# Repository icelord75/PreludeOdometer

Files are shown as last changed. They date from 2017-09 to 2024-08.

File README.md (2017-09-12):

# PreludeOdometer

Dot matrix LED display replacement for mechanical odometer in Honda Prelude IV

## Supported modes:
 - Arduino Nano328 controller
 - Precise configure wheel/VSS ratio
 - Total mileage
 - A/B trip (up to 9999.9km)
 - Motor hours counter
 - Configurable LED needle illumination with dimming feature
 - Configurable Electroluminescence instrumental cluster illumination controller
 - Outside Temperature (DS1820 sensor)

## License

**PreludeOdometer** is available under GPL License.

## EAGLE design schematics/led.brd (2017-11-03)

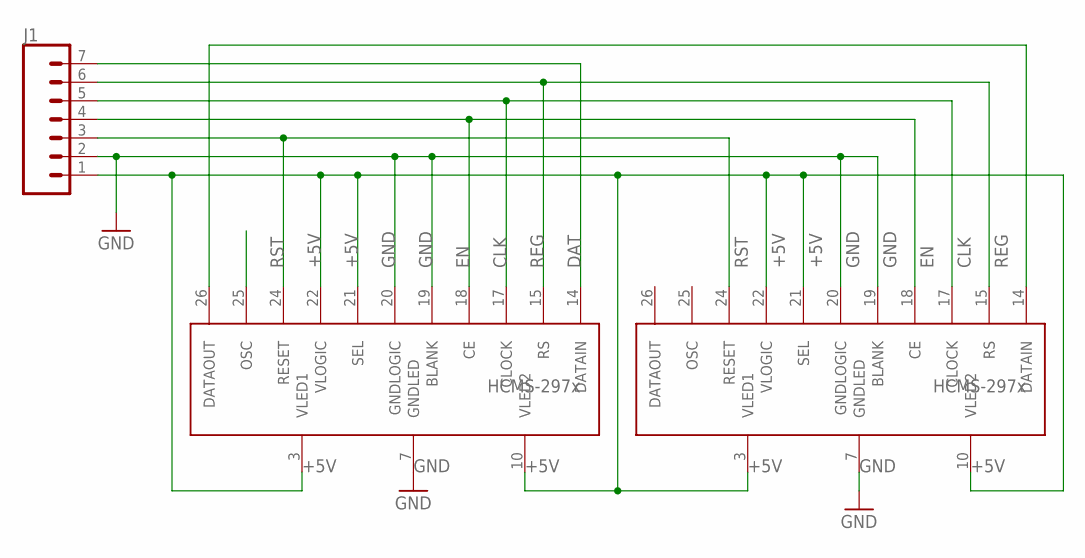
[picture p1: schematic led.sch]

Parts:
J1: CONN_07LONGPADS; 1X07_LONGPADS
U$1, U$2: HCMS-297X

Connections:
+5V: J1.1, U$1.3 (VLED1), U$1.10 (VLED2), U$1.21 (SEL), U$1.22 (VLOGIC), U$2.3 (VLED1), U$2.10 (VLED2), U$2.21 (SEL), U$2.22 (VLOGIC)
CLK: J1.5, U$1.17 (CLOCK), U$2.17 (CLOCK)
DAT: J1.7, U$1.14 (DATAIN)
EN: J1.4, U$1.18 (CE), U$2.18 (CE)
GND: J1.2, U$1.7 (GNDLED), U$1.19 (BLANK), U$1.20 (GNDLOGIC), U$2.7 (GNDLED), U$2.19 (BLANK), U$2.20 (GNDLOGIC)
unnamed: U$1.26 (DATAOUT), U$2.14 (DATAIN)
REG: J1.6, U$1.15 (RS), U$2.15 (RS)
RST: J1.3, U$1.24 (RESET), U$2.24 (RESET)

Board: 2 copper layers, 3 parts (0 on the bottom side), 8 nets, no tracks yet.

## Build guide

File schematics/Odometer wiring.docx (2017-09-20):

# MAIN BOARD

# 2 Pin SETUP BUTTON

1. Setup button
2. Setup button

# 3 Pin 1WIRE SENSOR

1. +5V
2. GND
3. 1WIRE

# 6 Pin CONNECTION BOARD

1. Button
2. LED DAT
3. LED REG
4. LED CLK
5. LED EN
6. LED RST

# 7 Pin CONNECTION BOARD

1. +12 IN
2. +5 OUT
3. DIM IN
4. VSS IN
5. NEEDLE CTL OUT
6. INDIGLO CTL OUT
7. GND

# CONNECTION BOARD

# 4 Pin GAUGES

1. +12 IN
2. DIM IN
3. VSS IN
4. GND IN

# 2 Pin NEEDLE

1. GND OUT
2. +5 OUT

# 3 Pin INDIGLO

1. N/C
2. GND OUT
3. +12 OUT

# 2 Pin #2 GAUGE BUTTON (next to 7PIN)

1. Button
2. Button

# 7 Pin LED MATRIX Display

1. +5V OUT
2. GND
3. LED RES
4. LED EN
5. LED CLK
6. LED REG
7. LED DAT

# 8 Pin MAIN BOARD

1. +12 OUT
2. +5 IN
3. VSS OUT
4. DIM OUT
5. NEEDLE CTL OUT
6. INDIGLO CTL OUT
7. –
8. GND

# 6 Pin MAIN BOARD

1. Button
2. LED DAT
3. LED REG
4. LED CLK
5. LED EN
6. LED RES

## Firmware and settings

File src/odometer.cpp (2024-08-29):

/*
   //      _______ __  _________ _________
   //      \_     |  |/  .  \   |   \ ___/
   //        / :  |   \  /   \  |   / _>_
   //       /      \ | \ |   /  |  /     \
   //      /   |___/___/____/ \___/_     /
   //      \___/--------TECH--------\___/
   //        ==== ABOVE SINCE 1994 ====
   //
   //   Ab0VE TECH - HONDA Prelude Odometer
 */

/* Controller connections
   //            +-----------+
   //            • TX    Vin •
   //            • RX  A Gnd •  <- GND
   //            • RST R RST •
   //     GND -> • GND D  +5 •  <- +5V Reg. LM2596HV
   //     VSS -> • 2   U  A7 •
   //     RPM -> • 3   I  A6 •
   // LED DAT <- • 4   N  A5 • -> FRAM SCL
   // LED Reg <- • 5   O  A4 • -> FRAM SDA
   // LED Clk <- • 6      A3 •
   //  LED En <- • 7   N  A2 •
   // LED RST -> • 8   A  A1 •
   //  Needle <- • 9   N  A0 • <- DIMMING
   // Indiglo <- • 10  O Arf •
   //   Setup -> • 11    3V3 •
   //  Button -> • 12 ||| 13 • <- OneWire DS1820
   //            +-----------+
 */

// TODO
//   racelogic bum edition )))
//   longterm l/100km
//   instant l/100km

//#define DEBUG

#include <avr/pgmspace.h>
#include <Arduino.h>
#include <LedDisplay.h>
#include <FM24.h>
#include <OneWire.h> // platformio lib install "OneWire"

#define disk1 0x50 // page of FM24C

OneWire ds(13); // DS1820 Temperature sensor

#define PPR 4 // VSS pulses per axle revolution

#define TRIP_A 0
#define TRIP_B 1
#define MOTOR_HOUR 2
#define OUTSIDE_TEMP 3

#define MAX_SHOW 3

// default tire size 205/55R15
#define TIRE_WIDTH_DEFAULT 4
#define TIRE_SIDE_DEFAULT 6
#define TIRE_RIM_DEFAULT 2

uint16_t TIRE_WIDTH_ARRAY[] = {165, 175, 185, 195, 205, 215, 225, 235, 245, 255, 265, 275, 285, 295, 305};
uint8_t TIRE_SIDE_ARRAY[] = {25, 30, 35, 40, 45, 50, 55, 60, 65, 70, 75, 80, 85};
uint8_t TIRE_RIM_ARRAY[] = {13, 14, 15, 16, 17, 18, 19, 20, 21, 22};

#define CONFIG_POS_MAX 11

// CONFIG
uint8_t TIRE_RIM;
uint8_t TIRE_WIDTH;
uint8_t TIRE_SIDE;
#define NEEDLE_STEP 16
#define NEEDLE_DIMMED_DEFAULT 127
#define NEEDLE_UNDIMMED_DEFAULT 255
uint8_t NEEDLE_DIMMED;
uint8_t NEEDLE_UNDIMMED;

#define MIN_DISPLAY 1 // Minimal visiable display
#define MAX_DISPLAY 15
#define DISPLAY_DIMMED_DEFAULT 10
#define DISPLAY_UNDIMMED_DEFAULT 15
uint8_t DISPLAY_DIMMED;
uint8_t DISPLAY_UNDIMMED;

#define INDIGLO_STEP 16
#define INDIGLO_DIMMED_DEFAULT 127
#define INDIGLO_UNDIMMED_DEFAULT 255
uint8_t INDIGLO_DIMMED;
uint8_t INDIGLO_UNDIMMED;

double TOTAL_TRIP;
double DAILY_TRIP_A;
double DAILY_TRIP_B;
int CURRENT_SHOW = TRIP_A;
boolean LEADING_ZERO;

// VSS input pin
#define VSS_PIN 2
unsigned int PULSES = 0;
float LENPERPULSE = 0;

// RPM input pin
#define RPM_PIN 3
volatile unsigned int RPM_COUNT = 0;
unsigned long timeold = 0;
unsigned int RPMs = 0;
float MOTOR_TIME;
unsigned int NOMINAL_RPM; // RPM with 1 hour == 1 motor hour
#define MAX_NOMINAL 6000
#define NOMINAL_STEP 200
float MOTOR_HOURS;
uint16_t MOTOR_HOURS_LIMIT;
#define DEFAULT_MOTOR_HOURS_LIMIT 200
#define MOTOR_HOURS_STEP 10
#define MAX_MOTOR_HOURS 1000
boolean LIMIT_BLINK = true;
uint8_t DIMMING;

// PINS CONFIG
#define BUTTON 12
#define NEEDLE 9
#define DIMPIN 14 // A0 as DIGITAL_PIN
#define SETUP_PIN 11
#define INDIGLO 10

#define LED_dataPin 4
#define LED_registerSelect 5
#define LED_clockPin 6
#define LED_enable 7
#define LED_reset 8
#define LED_displayLength 16 // Two HCMS-297x led matrix displays
LedDisplay myDisplay = LedDisplay(LED_dataPin, LED_registerSelect, LED_clockPin, LED_enable,
                                  LED_reset, LED_displayLength);

#define LOGO_DELAY 500 // first logo output delay
#define LONGPRESS_TIME 1000

float LEN = 0;
float TIRE_CIRCUMFERENCE;
float TEMPERATURE = 0;
unsigned long TIME, TIMES;
char buffer[20];
bool PRESSED = false;
bool LONGPRESS = false;
bool DIM = false;
bool DIMMED = true;
bool SETUP_PRESSED = false;
bool SETUP_DO = false;
uint8_t val;
uint8_t SETUP_POS = 0;
uint8_t data[12];
uint8_t addr[8];
uint8_t type_s;

#define DISPLAY_TRIP 0
#define DISPLAY_SETUP 1
uint8_t DISPLAY_MODE = DISPLAY_TRIP;
uint8_t DEFAULT_BRIGHTNESS;
uint8_t DEFAULT_NEEDLE;
uint8_t DEFAULT_INDIGLO;

bool result = false;

void CalcTire()
{
        TIRE_CIRCUMFERENCE = (TIRE_WIDTH_ARRAY[TIRE_WIDTH] * TIRE_SIDE_ARRAY[TIRE_SIDE] / 100 + TIRE_RIM_ARRAY[TIRE_RIM] * 25.4) * 3.1416 / 1000;
        LENPERPULSE = TIRE_CIRCUMFERENCE / PPR; // in Meters
#ifdef DEBUG
        Serial.print("TIRE CIRCUMFERENCE: ");
        Serial.print(TIRE_CIRCUMFERENCE);
        Serial.println("m");
        Serial.print("LEN PER PULSE: ");
        Serial.print(LENPERPULSE);
        Serial.println("m");
#endif
}

void VSS() // VSS signal interrupt
{
        PULSES++;
}

void RPM() // VSS signal interrupt
{
        RPM_COUNT++;
}

void setBrightness(uint8_t bright)
{
        // set the brightness: for each 4 chars
        for (int a = 1; a < LED_displayLength / 4; a++)
                myDisplay.loadControlRegister(B01110000 + (bright & B00001111));
}

void setup()
{
        Serial.begin(115200);
        Serial.print("\n\nAb0VE-TECH\nHonda Prelude Oddometer\n\n");
#ifdef DEBUG
        Serial.print("Connecting EEPROM...");
#endif
        twi_start();
#ifdef DEBUG
        Serial.print("OK\n");
#endif
        myDisplay.begin();
        setBrightness(0);
        pinMode(DIMPIN, INPUT);
        pinMode(NEEDLE, OUTPUT);
        pinMode(INDIGLO, OUTPUT);
        pinMode(BUTTON, INPUT_PULLUP);
        pinMode(SETUP_PIN, INPUT_PULLUP);
        pinMode(VSS_PIN, INPUT_PULLUP);
        pinMode(RPM_PIN, INPUT_PULLUP);

        attachInterrupt(digitalPinToInterrupt(VSS_PIN), VSS, RISING);  // positive tiggering
        attachInterrupt(digitalPinToInterrupt(RPM_PIN), RPM, FALLING); // negative tiggering

        // Start DS
        if (!ds.search(addr))
                ds.reset_search();
        if (addr[0] == 0x10)
                type_s = 1;
        else
                type_s = 0;
        ds.reset();
        ds.select(addr);
        ds.write(0x44, 1);

#ifdef DEBUG
        Serial.print("Reading config...");
#endif
        // read config from EEPROM
        result = FM24C_read(disk1, 0, (uint8_t *)&TOTAL_TRIP, 4);
        result = FM24C_read(disk1, 4, (uint8_t *)&DAILY_TRIP_A, 4);
        result = FM24C_read(disk1, 9, (uint8_t *)&DAILY_TRIP_B, 4);
        result = FM24C_read(disk1, 200, (uint8_t *)&CURRENT_SHOW, 1);
        result = FM24C_read(disk1, 37, (uint8_t *)&TIRE_WIDTH, 1);
        result = FM24C_read(disk1, 18, (uint8_t *)&TIRE_SIDE, 1);
        result = FM24C_read(disk1, 19, (uint8_t *)&TIRE_RIM, 1);
        result = FM24C_read(disk1, 20, (uint8_t *)&NEEDLE_DIMMED, 1);
        result = FM24C_read(disk1, 21, (uint8_t *)&NEEDLE_UNDIMMED, 1);
        result = FM24C_read(disk1, 22, (uint8_t *)&DISPLAY_DIMMED, 1);
        result = FM24C_read(disk1, 23, (uint8_t *)&DISPLAY_UNDIMMED, 1);
        result = FM24C_read(disk1, 24, (uint8_t *)&MOTOR_HOURS, 4);
        result = FM24C_read(disk1, 28, (uint8_t *)&NOMINAL_RPM, 4);
        result = FM24C_read(disk1, 32, (uint8_t *)&MOTOR_HOURS_LIMIT, 2);
        result = FM24C_read(disk1, 34, (uint8_t *)&LEADING_ZERO, 1);
        result = FM24C_read(disk1, 35, (uint8_t *)&INDIGLO_DIMMED, 1);
        result = FM24C_read(disk1, 36, (uint8_t *)&INDIGLO_UNDIMMED, 1);

#ifdef DEBUG
        Serial.print("EEPROM TOTAL: ");
        Serial.print(TOTAL_TRIP);
        Serial.print(", A: ");
        Serial.print(DAILY_TRIP_A);
        Serial.print(", B: ");
        Serial.print(DAILY_TRIP_B);
        Serial.print('\n');
        Serial.print("EEPROM TIRES: ");
        Serial.print(TIRE_WIDTH);
        Serial.print("/");
        Serial.print(TIRE_SIDE);
        Serial.print("R");
        Serial.print(TIRE_RIM);
        Serial.print('\n');
        Serial.print("EEPROM NEEDLE Day:");
        Serial.print(NEEDLE_UNDIMMED);
        Serial.print(" Night:");
        Serial.print(NEEDLE_DIMMED);
        Serial.print('\n');
        Serial.print("EEPROM DISPLAY: Day:");
        Serial.print(DISPLAY_UNDIMMED);
        Serial.print(" Night:");
        Serial.print(DISPLAY_DIMMED);
        Serial.print('\n');
        Serial.print("EEPROM INDIGLO: Day:");
        Serial.print(INDIGLO_UNDIMMED);
        Serial.print(" Night:");
        Serial.print(INDIGLO_DIMMED);
        Serial.print('\n');
        Serial.print("EEPROM MOTOR: Hours");
        Serial.print(MOTOR_HOURS);
        Serial.print(" RPM:");
        Serial.print(NOMINAL_RPM);
        Serial.print(" Limit:");
        Serial.print(MOTOR_HOURS_LIMIT);
        Serial.print('\n');
#endif

        // fix posible eeprom errata
        if ((TOTAL_TRIP < 0) && (TOTAL_TRIP > 99999999))
                TOTAL_TRIP = 0;
        if (DAILY_TRIP_A < 0)
                DAILY_TRIP_A = 0;
        if (DAILY_TRIP_B < 0)
                DAILY_TRIP_B = 0;
        if (TIRE_WIDTH >= sizeof(TIRE_WIDTH_ARRAY) / 2)
                TIRE_WIDTH = TIRE_WIDTH_DEFAULT;
        if (TIRE_SIDE >= sizeof(TIRE_SIDE_ARRAY))
                TIRE_SIDE = TIRE_SIDE_DEFAULT;
        if (TIRE_RIM >= sizeof(TIRE_RIM_ARRAY))
                TIRE_RIM = TIRE_RIM_DEFAULT;
        if (NEEDLE_DIMMED < 1)
                NEEDLE_DIMMED = NEEDLE_DIMMED_DEFAULT;
        if (NEEDLE_UNDIMMED < 1)
                NEEDLE_UNDIMMED = NEEDLE_UNDIMMED_DEFAULT;
        if (DISPLAY_DIMMED < 1)
                DISPLAY_DIMMED = DISPLAY_DIMMED_DEFAULT;
        if (DISPLAY_UNDIMMED < 1)
                DISPLAY_UNDIMMED = DISPLAY_UNDIMMED_DEFAULT;
        if (INDIGLO_DIMMED < 1)
                INDIGLO_DIMMED = INDIGLO_DIMMED_DEFAULT;
        if (INDIGLO_UNDIMMED < 1)
                INDIGLO_UNDIMMED = INDIGLO_UNDIMMED_DEFAULT;
        if (NOMINAL_RPM < 500)
                NOMINAL_RPM = 2000;
        if (MOTOR_HOURS_LIMIT < 100)
                MOTOR_HOURS_LIMIT = DEFAULT_MOTOR_HOURS_LIMIT;
        LEADING_ZERO = LEADING_ZERO & 1;
        if (CURRENT_SHOW > MAX_SHOW)
                CURRENT_SHOW = 0;

        CalcTire();
#ifdef DEBUG
        Serial.print("\nHere we go...\n");
#endif
        myDisplay.home();
        setBrightness(0);
        myDisplay.print("   HondaPrelude ");
        for (int a = 1; a <= DISPLAY_UNDIMMED; a++)
        {
                setBrightness(a);
                analogWrite(NEEDLE, a * 17);
                analogWrite(INDIGLO, a * 17);
                delay(20);
        }
        DEFAULT_BRIGHTNESS = DISPLAY_UNDIMMED;
        DEFAULT_NEEDLE = NEEDLE_UNDIMMED;
        DEFAULT_INDIGLO = INDIGLO_UNDIMMED;
        delay(LOGO_DELAY);
        DIMMED = true;
}

void ReadTemp()
{
        ds.reset();
        ds.select(addr);
        ds.write(0xBE);

        for (uint8_t i = 0; i < 9; i++)
                data[i] = ds.read();
        int16_t raw = (data[1] << 8) | data[0];
        if (type_s)
        {
                raw = raw << 3;
                if (data[7] == 0x10)
                        raw = (raw & 0xFFF0) + 12 - data[6];
        }
        else
        {
                byte cfg = (data[4] & 0x60);
                if (cfg == 0x00)
                        raw = raw & ~7;
                else if (cfg == 0x20)
                        raw = raw & ~3;
                else if (cfg == 0x40)
                        raw = raw & ~1;
        }
        TEMPERATURE = (float)raw / 16.0;
}

void loop()
{
        // Temperature
        ReadTemp();

        // RPM calculation
        if (RPM_COUNT != 0)
        {
                RPMs = (RPM_COUNT / (float)(millis() - timeold)) * 1000.0 * 60 / 4; // 4 pulses per one revolution
                MOTOR_TIME = RPMs / NOMINAL_RPM * (millis() - timeold) / 1000;      // in SEC
                RPM_COUNT = 0;
                timeold = millis();
                MOTOR_HOURS += MOTOR_TIME / 3600; // in HOURS
        }

        // TRIP calculation
        if (PULSES != 0)
        {
#ifdef DEBUG
                Serial.print("PULSES: ");
                Serial.print(PULSES);
                Serial.println("");
                Serial.print("TIRE CIRCUMFERENCE: ");
                Serial.print(TIRE_CIRCUMFERENCE);
                Serial.println("m");
#endif
                LEN = PULSES * LENPERPULSE;
                PULSES = 0;
                TOTAL_TRIP += LEN / 1000;   // in Km
                DAILY_TRIP_A += LEN / 1000; // in Km
                DAILY_TRIP_B += LEN / 1000; // in Km
                if (DAILY_TRIP_A >= 10000)
                        DAILY_TRIP_A -= 10000;
                if (DAILY_TRIP_B >= 10000)
                        DAILY_TRIP_B -= 10000;
        }

        /// Store in FRAM in each cycle
        result = FM24C_write(disk1, 0, (uint8_t *)&TOTAL_TRIP, 4);
        result = FM24C_write(disk1, 4, (uint8_t *)&DAILY_TRIP_A, 4);
        result = FM24C_write(disk1, 9, (uint8_t *)&DAILY_TRIP_B, 4);
        result = FM24C_write(disk1, 24, (uint8_t *)&MOTOR_HOURS, 4);

#ifdef DEBUG
        Serial.print("RPM:");
        Serial.print(RPMs);
        Serial.print(" T:");
        Serial.print(TOTAL_TRIP);
        Serial.print(" A:");
        Serial.print(DAILY_TRIP_A);
        Serial.print(" B:");
        Serial.print(DAILY_TRIP_B);
        Serial.print(" M:");
        Serial.print(MOTOR_HOURS);
        Serial.print(" TEMP:");
        Serial.print(TEMPERATURE);
        Serial.println("");
#endif

        DIMMING = digitalRead(DIMPIN);
        if (DIMMING == HIGH)
        {
                if (!DIMMED)
                { // JUST DIMMED and fade in
                        setBrightness(DISPLAY_DIMMED);
                        analogWrite(NEEDLE, NEEDLE_DIMMED);
                        analogWrite(INDIGLO, INDIGLO_DIMMED);
                        DIMMED = true;
                        /*                      if (DEFAULT_BRIGHTNESS > DISPLAY_DIMMED)
                                               {
                                                       DEFAULT_BRIGHTNESS--;
                                                       setBrightness(DEFAULT_BRIGHTNESS);
                                               }
                                               if (DEFAULT_NEEDLE > NEEDLE_DIMMED)
                                               {
                                                       DEFAULT_NEEDLE -= NEEDLE_STEP;
                                                       analogWrite(NEEDLE, DEFAULT_NEEDLE);
                                               }
                                               if (DEFAULT_INDIGLO > INDIGLO_DIMMED)
                                               {
                                                       DEFAULT_INDIGLO -= INDIGLO_STEP;
                                                       analogWrite(INDIGLO, DEFAULT_INDIGLO);
                                               }
                                               if ((DEFAULT_BRIGHTNESS = DISPLAY_DIMMED) && (DEFAULT_NEEDLE = NEEDLE_DIMMED) && (DEFAULT_INDIGLO = INDIGLO_DIMMED))
                                                       DIMMED = true;*/
                }
        }
        else
        {
                if (DIMMED)
                { // JUST UNDIMMED and fade out
                        setBrightness(DISPLAY_UNDIMMED);
                        analogWrite(NEEDLE, NEEDLE_UNDIMMED);
                        analogWrite(INDIGLO, INDIGLO_UNDIMMED);
                        DIMMED = false;
                        /*                        if (DEFAULT_BRIGHTNESS < DISPLAY_UNDIMMED)
                                                {
                                                        DEFAULT_BRIGHTNESS++;
                                                        setBrightness(DEFAULT_BRIGHTNESS);
                                                }
                                                if (DEFAULT_NEEDLE < NEEDLE_UNDIMMED)
                                                {
                                                        DEFAULT_NEEDLE += NEEDLE_STEP;
                                                }
                                                analogWrite(NEEDLE, DEFAULT_NEEDLE);
                                                if (DEFAULT_INDIGLO < INDIGLO_UNDIMMED)
                                                {
                                                        DEFAULT_INDIGLO += INDIGLO_STEP;
                                                        analogWrite(INDIGLO, DEFAULT_INDIGLO);
                                                }
                                                if ((DEFAULT_BRIGHTNESS = DISPLAY_UNDIMMED) && (DEFAULT_NEEDLE = NEEDLE_UNDIMMED) && (DEFAULT_INDIGLO = INDIGLO_UNDIMMED))
                                                        DIMMED = false;*/
                }
        }

        val = digitalRead(SETUP_PIN);
        if (val == LOW)
        {
                if (!SETUP_PRESSED)
                {
                        SETUP_PRESSED = true;
                        SETUP_DO = true;
                        TIMES = millis();
                }
                else
                {
                        if ((millis() - TIMES) > LONGPRESS_TIME)
                        {
                                TIMES = millis();
                                switch (DISPLAY_MODE)
                                {
                                case DISPLAY_TRIP:
                                        DISPLAY_MODE = DISPLAY_SETUP;
                                        SETUP_DO = false;
                                        break;
                                default:
                                        // BACK FROM SETUP
                                        result = FM24C_write(disk1, 37, (uint8_t *)&TIRE_WIDTH, 1);
                                        result = FM24C_write(disk1, 18, (uint8_t *)&TIRE_SIDE, 1);
                                        result = FM24C_write(disk1, 19, (uint8_t *)&TIRE_RIM, 1);
                                        result = FM24C_write(disk1, 20, (uint8_t *)&NEEDLE_DIMMED, 1);
                                        result = FM24C_write(disk1, 21, (uint8_t *)&NEEDLE_UNDIMMED, 1);
                                        result = FM24C_write(disk1, 22, (uint8_t *)&DISPLAY_DIMMED, 1);
                                        result = FM24C_write(disk1, 23, (uint8_t *)&DISPLAY_UNDIMMED, 1);
                                        result = FM24C_write(disk1, 28, (uint8_t *)&NOMINAL_RPM, 4);
                                        result = FM24C_write(disk1, 32, (uint8_t *)&MOTOR_HOURS_LIMIT, 2);
                                        result = FM24C_write(disk1, 34, (uint8_t *)&LEADING_ZERO, 1);
                                        result = FM24C_write(disk1, 35, (uint8_t *)&INDIGLO_DIMMED, 1);
                                        result = FM24C_write(disk1, 36, (uint8_t *)&INDIGLO_UNDIMMED, 1);
                                        DISPLAY_MODE = DISPLAY_TRIP;
                                        SETUP_DO = false;
                                        CalcTire(); // Recalc circumference size
                                        break;
                                }
                        }
                }
        }
        else
        {
                SETUP_PRESSED = false;
        }

        switch (DISPLAY_MODE)
        {
                // TRIP MODE
        case DISPLAY_TRIP:
                val = digitalRead(BUTTON);
                if (val == LOW)
                {
                        if (!PRESSED)
                        { // JUST PRESSED
#ifdef DEBUG
                                Serial.println("MODE CHANGE");
#endif
                                PRESSED = true;
                                TIME = millis();
                        }
                        else
                        { // HOLDING
                                if ((millis() - TIME) > LONGPRESS_TIME)
                                { // LOGPRESS
                                        LONGPRESS = true;
                                        switch (CURRENT_SHOW)
                                        {
                                        case TRIP_A:
                                                DAILY_TRIP_A = 0;
                                                break;
                                        case TRIP_B:
                                                DAILY_TRIP_B = 0;
                                                break;
                                        case MOTOR_HOUR:
                                                MOTOR_HOURS = 0;
                                                break;
                                        }
                                }
                        }
                }
                else
                {
                        if (PRESSED) // JUST RELEASED
                        {
                                PRESSED = false;
                                if (!LONGPRESS)
                                { // SHORTPRESS
                                        CURRENT_SHOW++;
                                        if (CURRENT_SHOW > MAX_SHOW)
                                                CURRENT_SHOW = 0; // A/B/H/T
                                        result = FM24C_write(disk1, 200, (uint8_t *)&CURRENT_SHOW, 2);
                                }
                                else
                                        LONGPRESS = false;
                        }
                }
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

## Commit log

2017-08-24 updates motor hours counter
2017-08-26 Cross board schematics
    [Connections.sch]
2017-08-27 updates fix multi devices brightness
2017-08-27 LED Display text fitting
2017-09-12 add tem sensor and minor fixes
2017-09-20 LedDisplay moved internaly + font mods
2017-09-20 minor updates
    [gauges_ser.brd, gauges_ser.sch]
2017-09-20 boards wiring added
2017-09-21 schematics addon
    [gauges_ser.brd, led.sch]

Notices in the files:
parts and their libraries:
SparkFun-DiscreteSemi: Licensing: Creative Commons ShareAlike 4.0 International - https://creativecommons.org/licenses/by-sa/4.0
